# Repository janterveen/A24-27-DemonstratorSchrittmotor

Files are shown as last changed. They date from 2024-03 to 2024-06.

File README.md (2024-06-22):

<div>
  <p>
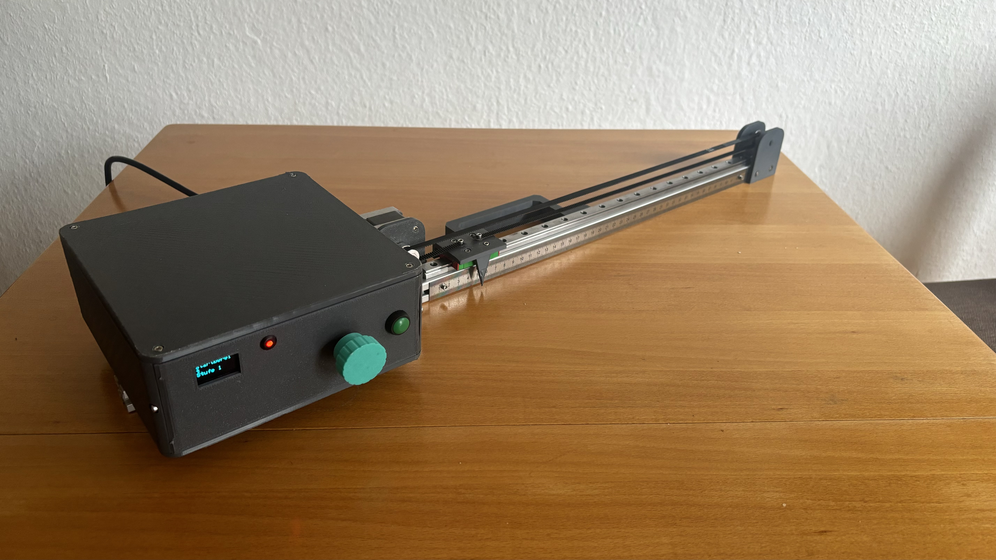
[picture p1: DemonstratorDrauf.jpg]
    
  </p>
  <b><h3> Automatisierungstechnik Projekt aus dem Jahr 2024 </h3></b>
  <p> Demonstrator für einen Schrittmotor mit <a href="https://www.arduino.cc"> Arduino-Ansteuerung </a></p>
</div>
<br>

# Betreuer: Prof. Dr. Elmar Wings

# Autoren (Name, Vorname, Matrikelnummer):

1. ter Veen, Jan, 7022071
2. Stein, Enno, 7021960
3. Theilmann, Maik, 7021861
4. Hanneken, Lars, 7021910
5. Grönke, Jannik, 7022006

# Projektbeschreibung: 
Die Aufgabe besteht darin, mithilfe eines Arduino Nano 33 BLE Sense Lite einen Demonstrator für einen Schrittmotor zu entwickeln. 
Mittels einer Konstruktion, die einen Schrittmotor beinhaltet, welcher einen Riemen antreibt, soll ein Schlitten auf einer Linearführung verfahren werden. 
Es sollen unterschiedliche Bewegungscharaketeristiken demonstriert werden. Der Schrittmotor wird über den Arduino angesteuert und in die gewünschte Richtung und Position bewegt. 

# Verzeichnisstruktur: 
## Autor, Projektplan und README
- [Author-Excel](author.xlsx)
  - Excel-Datei in der persönliche Daten über die einzelnen Gruppenmitglieder wiederzufinden sind
- [Projektplan-Excel](Projektplan.xlsx)
  - Excel-Datei die während des Projekts zur Projektplanung diente
- [README](README.md)
- [Evaluation](EvaluationHW.xlsx)

## Anhang
- [Konstruktion](DemonstratorSchrittmotor/Appendix/Konstruktion)
  - Sämtliche Zur Konstruktion benötigten Dateien, wie CAD-Dateien, G-Code und STL-Dateien
- [Material-Rückgabeliste](DemonstratorSchrittmotor/Appendix/MaterialRuekgabeListe)
  - Auflistung der nicht verwendeten Teilen
- [Mindmap](DemonstratorSchrittmotor/Appendix/Mindmap)
- [Schaltplan](DemonstratorSchrittmotor/Appendix/SchaltplanFritzing)

## Montageanleitung (sämtliche Inhalte und die verwendeten Bilder)
- [Montageanleitung](DemonstratorSchrittmotor/Assembly)
- [Inhalte](DemonstratorSchrittmotor/Assembly/Chapters)
  - Ort an dem sich die Tex-Dateien für die einzelnen Kapiteln der Montageanleitung befinden
- [Gestaltung](DemonstratorSchrittmotor/Assembly/General)
  - In diesem Ordner sind Dateien, zur Gestaltung der Montageanleitung
- [Bilder](DemonstratorSchrittmotor/Assembly/Images)
  - Ablage der Bilder, die in der Montageanleitung benutzt werden
- [PDF](DemonstratorSchrittmotor/Assembly/MontageAnleitung.pdf)

## verwendeter Code
- [Code](DemonstratorSchrittmotor/Code)
- [Arduino](DemonstratorSchrittmotor/Code/Arduino)
 - Testprogramm für den Arduino
- [DemonstratorSchrittmotor](DemonstratorSchrittmotor/Code/DemonstratorSchrittmotor)
 - Fertiges Programm für den Arduino
- [Encoder](DemonstratorSchrittmotor/Code/Encoder)
 - Testprogramm für den Encoder
- [html](DemonstratorSchrittmotor/Code/html)
 - Ordner für die doxygen Dokumentation
- [latex](DemonstratorSchrittmotor/Code/latex)
 - Ordner für die doxygen Dokumentation als Latex-Code
- [LED](DemonstratorSchrittmotor/Code/LED)
 - Testprogramm für die LED
- [OLEDDisplay](DemonstratorSchrittmotor/Code/OLEDDisplay)
 - Testprogramm für das OLED Display
- [Stepper](DemonstratorSchrittmotor/Code/Stepper)
 - Testprogramm für den Stepper
- [Taster](DemonstratorSchrittmotor/Code/Taster)
 - Testprogramm für den Taster
- [TastermitDebounce](DemonstratorSchrittmotor/Code/TastermitDebounce)
 - Testprogramm für den Taster mit Debounce

## Service- und Entwicklerdocumentation
- [Service- und Entwicklerdocumentation](DemonstratorSchrittmotor/DeveloperDoc)
- [Inhalte](DemonstratorSchrittmotor/DeveloperDoc/Chapters)
  - Ort an dem sich die Tex-Dateien für die einzelnen Kapiteln der Service- und Entwicklerdocumentation befinden
- [Gestaltung](DemonstratorSchrittmotor/DeveloperDoc/General)
  - In diesem Ordner sind Dateien, zur Gestaltung der Service- und Entwicklerdocumentation
- [Bilder](DemonstratorSchrittmotor/DeveloperDoc/Images)
  - Ablage der Bilder, die in der Service- und Entwicklerdocumentation benutzt werden
- [Tikz](DemonstratorSchrittmotor/DeveloperDoc/tikz)
  - Tex-Dateien zur Ersetllung von Tikz-Diagrammen oder Zeichnungen
- [Service- und Entwicklerdocumentation-PDF](DemonstratorSchrittmotor/DeveloperDoc/DemonstratorSchrittmotor.pdf)

## Demontageanleitung (sämtliche Inhalte und die verwendeten Bilder)
- [Demontageanleitung](DemonstratorSchrittmotor/Disassembly)
- [Inhalte](DemonstratorSchrittmotor/Disassembly/Chapters)
  - Ort an dem sich die Tex-Dateien für die einzelnen Kapiteln der Demontageanleitung befinden
- [Gestaltung](DemonstratorSchrittmotor/Disassembly/General)
  - In diesem Ordner sind Dateien, zur Gestaltung der Demontageanleitung
- [Bilder](DemonstratorSchrittmotor/Disassembly/Images)
  - Ablage der Bilder, die in der Demontageanleitung benutzt werden
- [PDF](DemonstratorSchrittmotor/Disassembly/DemontageAnleitung.pdf)
  
## verwendete Quellen und bib-file (Datenblätter und Literatur in PDF)
- [Dokumente](DemonstratorSchrittmotor/Documents)
- [Arduino IDE Dokumentation](DemonstratorSchrittmotor/Documents/ArduinoIDEDoku)
  - Quellen für die Softwaredokumentation von der Arduino Website
- [Datenblätter](DemonstratorSchrittmotor/Documents/Datenblätter)
  - Unter diesem Pfad befinden sich die Datenblätter, die für die Dokumentation benötigt wurden
- [Literatur](DemonstratorSchrittmotor/Documents/Literatur)
  - Hier befindet sich die verwendete Literatur
- [Bildquellen der Materialliste](DemonstratorSchrittmotor/Documents/MateriallisteQuellen)
- [Bibliothek](DemonstratorSchrittmotor/Documents/MyLiterature.bib)
  - Citavi Bibliothek mit allen genutzten Quelleinträgen

## Das Handbuch für den Demonstrator (sämtliche Inhalte und die verwendeten Bilder)
- [Handbuch](DemonstratorSchrittmotor/Manual)
- [Inhalte](DemonstratorSchrittmotor/Manual/Chapters)
  - Ort an dem sich die Tex-Dateien für die einzelnen Kapitel des Handbuches befinden
- [Gestaltung](DemonstratorSchrittmotor/Manual/General)
  - In diesem Ordner sind Dateien, zur Gestaltung des Handbuches
- [Bilder](DemonstratorSchrittmotor/Manual/Images)
  - Ablage der Bilder, die im Handbuch benutzt werden
- [Handbuch-PDF](DemonstratorSchrittmotor/Manual/HandbuchDemonstratorSchrittmotor.pdf)

## Das Poster zum Projekt (sämtliche Inhalte und die verwendeten Bilder)
- [Poster](DemonstratorSchrittmotor/Poster)
- [Bilder](DemonstratorSchrittmotor/Poster/images)
  - Ablage der Bilder, die im Poster benutzt werden
- [Poster-PDF](DemonstratorSchrittmotor/Poster/tikzposter.pdf)

## Literaturverzeichnis als Präsentation
- [Bilder](DemonstratorSchrittmotor/Presentations/images)
  - Coverbilder der Quellen
- [Hintergrundbilder](DemonstratorSchrittmotor/Presentations/img)
- [Folien](DemonstratorSchrittmotor/Presentations/slides)
- [Literaturverzeichnis-PDF](DemonstratorSchrittmotor/Presentations/Literaturverzeichnis.pdf)

## Schnelleinstieg
- [Schnelleinstieg-PDF](DemonstratorSchrittmotor/Presentations/Literaturverzeichnis.pdf)

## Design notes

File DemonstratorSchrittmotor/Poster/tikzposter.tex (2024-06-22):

%%%%%%
% $Beschreibung: Poster des Demonstrators mit erklärung eines Schrittmotors $
% $Autor: Groenke $
% $Datum: 18.06.2024 $
% $Version: 1 $
% $Pfad: SchrittmotorArduino/Poster/tikzposter.tex $
%
%%%%%%

\documentclass[25pt,a0paper, portrait]{tikzposter}
\usepackage[utf8]{inputenc}
\usepackage{xcolor}
\usepackage{graphicx,mwe}
\usepackage{filecontents}
\usepackage{lipsum}
\usepackage{tikz}
\usepackage{multicol}
\usepackage{adjustbox}
\usepackage{blindtext}
\usepackage{comment}

 \makeatletter
\def\TP@titlegraphictotitledistance{-6cm}
\settitle{ \centering \vbox{
		\@titlegraphic \\ [\TP@titlegraphictotitledistance] 
		\centering
		\color{titlefgcolor} 
		{\bfseries \Huge \sc \@title \par}
		\vspace*{1em}
		{\huge \@author \par}
}}
\makeatother

\setlength{\columnsep}{2cm}
 
\title{Schrittmotor Demonstrator}
\author{A24-27}
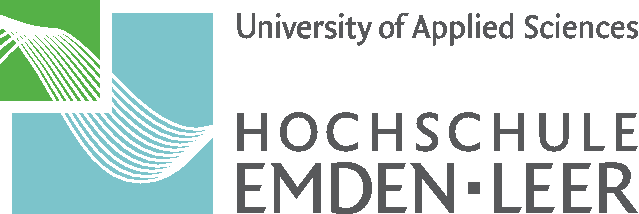
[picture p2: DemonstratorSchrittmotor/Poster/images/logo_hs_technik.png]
\titlegraphic{
	\hfill

}

\usetheme{Desert}
 
\begin{document}

\maketitle

\begin{columns} 
	
	\column{0.4}
	{
		\colorlet{blocktitlebgcolor}{blue}
		\block{Demonstrator für einen Schrittmotor}
		{
			\begin{tikzfigure}
				
			\end{tikzfigure}	
		}
		\block{Schrittmotoren}
		{
			Ein Schrittmotor ist ein Elektromotor, der sich für präzise Positionierungsaufgaben eignet. Im Gegenteil zu anderen Elektromotoren wird bei einem Schrittmotor keine Positionsmessung oder Positionsregelung benötigt. Mit diesem Motor ist eine erreichbare Positioniergenauigkeit von 0,1° möglich. Diese Art von Elektromotor wird beispielsweise in Druckern oder Scanner, aber auch im Kraftfahrzeugbereich verwendet. Im Kraftfahrzeugbereich werden die Schrittmotoren zur Spiegelverstellung sowie der Sitzverstellung verwendet. Das maximal erreichbare Drehmoment eines Schrittmotors liegt bei zwei Newtonmeter und die maximal erreichbare Drehzahl bei ca. 2000 Umdrehung pro Minute. Ein großer Vorteil des Schrittmotors ist seine Wartungsfreiheit, da der Rotor keine Wicklungen hat. [Babiel 2023, Hagl 2021]
		}
	}

	\column{0.6}
	{
		\colorlet{blocktitlebgcolor}{blue}
		\block{Projektbeschreibung}
		{
			Mithilfe eines Arduino Nano 33 BLE Sense Lite wurde dieser Demonstrator für einen Schrittmotor entwickelt. Mittels einer Konstruktion, die über einen Schrittmotor verfügt, wird ein Riemen angetrieben. An diesem Riemen ist ein Schlitten befestigt, der durch die Bewegung des Schrittmotors auf einer Linearführung verfahren wird. An dem Gehäuse befindet sich ein Drehschalter, mit dem eine von zehn Bewegungsstufen ausgewählt werden kann. Nach der Auswahl kann das Programm über den grünen Start-Stopp-Knopf gestartet werden. Die Status-LED leuchtet rot, sobald das Gerät einsatzbereit ist. Für die Referenzfahrt wurde ein Endschalter an der Halterung des Schrittmotors befestigt, damit der Schrittmotor auf eine definierte Position referenzieren kann. Es gibt zehn verschiedene Bewegungsstufen. Die Bewegungsstufen unterscheiden sich in der Geschwindigkeit. Pro Stufe wird die Geschwindigkeit erhöht.
			Ein großer Teil der Bauteile wurde mit einem 3D-Drucker gefertigt. So konnten Gehäuse, Drehschalter, Zeiger (auf dem Schlitten), Halterungen, sowie ein Griff selbst konstruiert und angepasst werden. 
		}
		\block{Nema 17 Schrittmotor}
		{
			Für dieses Projekt wird ein Nema 17 Schrittmotor der Firma Creality3D verwendet. Dieser Schrittmotor wird im 3D-Druck sowie in CNC-Maschinen eingesetzt. Der Motor arbeitet im Bipolarbetrieb und es sind zwei Spulen verbaut. Er hat einen Schrittwinkel von 1,8 ° und
			benötigt somit 200 Schritte für eine volle Umdrehung. Die Wellenlänge beträgt 20 mm und der Wellendurchmesser 5 mm. Der ausgewählte Schrittmotor arbeitet mit einer Nennspannung von 12 Volt. Dadurch, dass er mit einer niedrigen Spannung arbeitet, kann kein hohes Drehmoment erzeugt werden. Allerdings erzielt der Schrittmotor eine gute Positioniergenauigkeit durch den kleinen Schrittwinkel und die Microstepp-Funktion. Des Weiteren arbeitet der Motor mit 0,84 Amper pro Phase. Weitere Vorteile des Schrittmotors sind die kompakte Bauform mit den Abmessung 42 x 42 x 34 mm sowie die geringe Masse von 220 Gramm. Betrieben werden kann der Schrittmotor in einer Umgebungstemperatur von -20 °C bis +50 °C. [Gemsmotor 2024] 
		}
	}
\end{columns}

\begin{columns} 
	
	\column{0.4}
	{
		\colorlet{blocktitlebgcolor}{blue}
		\block{Nema 17 Schrittmotor}
		{
			\begin{tikzfigure}
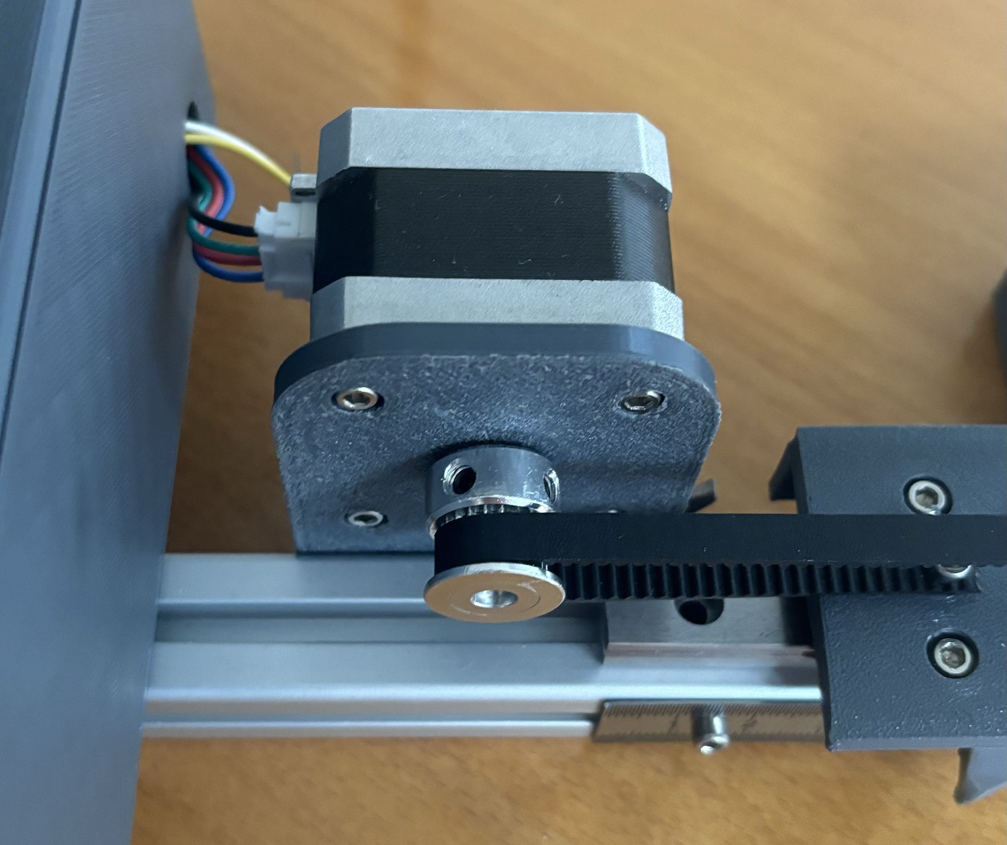
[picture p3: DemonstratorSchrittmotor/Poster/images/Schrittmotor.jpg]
				
			\end{tikzfigure}	
		}
		\block{Quellen}
		{
			\begin{itemize}
				\item R. Hagl. Elektrische Antriebstechnik. 3., überarbeitete und erweiterte Auflage. München: Hanser, 2021. isbn: 978-3-446-46572-5.
				\item G. Babiel. Elektrische Antriebe in der Fahrzeugtechnik: Lehrund Arbeitsbuch. 5. Auflage. Wiesbaden und Heidelberg: Springer Vieweg, 2023. isbn: 978-3-658-40585-4.
				\item Gemsmotor. Nema 17-Datasheet.
			\end{itemize}
		}
	}

	\column{0.6}
	{
		\colorlet{blocktitlebgcolor}{blue}
		\block{Herausforderungen}
		{
			Das Projekt lässt sich in drei verschiedene Teilprojekte unterteilen, die zum Abschluss der Aufgabe führen. Zuerst ist da die Konstruktion des Demonstrators und die hierfür benötigte Auswahl der Hardware-Teile. Vorgabe war, dass der Aufbau nicht zu komplex ist und man sich so auf die wesentlichen Teile konzentriert. Außerdem ist die Arbeit mit der Arduino IDE und die Programmierung des Arduino ein weiterer Teil. Als letzten Punkt ist der Umgang mit den elektronischen Bauteilen zu erwähnen. Der Umgang mit den elektronischen Bauteilen sollte unter großer Vorsicht geschehen, sodass diese nicht durch den elektrischen Strom beschädigt werden.
		}
		\block{Lösungsansatz}
		{
			Durch die Ausarbeitung der Herausforderungen, können Lösungsansätze	entwickelt werden. Vorab wurde eine erste Konzeptskizze angefertigt, aus der Ideen entstanden. Im ersten Konzept sollte der Schrittmotor eine Plattform über einen Riementrieb axial verfahren. Dabei sollte der Verfahrweg der Plattform über einen Abstandssensor mit einem vorher definierten Abstand zu einem Objekt, geregelt werden. Wird das Objekt näher oder weiter entfernt vom Abstandssensor bewegt, verfährt die Plattform mit einem definierten Abstand mit. Alle vorhandenen Bauteile sollten an einem Alu-Profil befestigt werden. Aufgrund der hohen Komplexität wurde die Plattform inklusive des Abstandssensors, aus dem zweiten Konzept entfernt. Stattdessen wird auf dem Schlitten der Linearführung, ein Zeiger und auf dem Alu-Profil, ein Lineal integriert. Mittels verschiedener Stufen soll der Schrittmotor unterschiedliche Geschwindigkeiten demonstrieren. Gegenüber dem zweiten Konzept wurde die Hardware aus Transportiergründen mit auf dem Aluprofil verlegt und erhielt zum Schutz ein Gehäuse.
		}
		\block{Zukünftige Projekte}
		{
			\begin{itemize}
				\item Aktive Geschwindigkeits- und Beschleunigungsregelung durch Beschleunigungssensor
				\item Manuelle Eingabe von Beschleunigung und Geschwindigkeit
				\item Manuelle Eingabe des Verfahrweges
			\end{itemize}
		}
	}
\end{columns}

\end{document}

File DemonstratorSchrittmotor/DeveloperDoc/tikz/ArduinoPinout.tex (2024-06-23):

%%%%%%
%
% $Autor: ter Veen $
% $Datum: 01.06.2024 $
% $Version: 1 $
% $Pfad: SchrittmotorArduino/DevoloperDoc/tikz/ArduinoPinout.tex $
%
%%%%%%
	\begin{tikzpicture}[scale=2]
		% Arduino Dummy
		\draw[fill=blue!20] (0,0) rectangle (6,3);
		
		% Pin Beschriftung oben
		\foreach \x in {0.375,1.125,...,5.625}
		\draw (\x,3) -- (\x,3.5) node[above] {};
		\foreach \x in {0.75,1.5,...,5.25}
		\draw (\x,3) -- (\x,3.25) node[above] {};
		
		% Pin Beschriftung unten
		\foreach \x in {0.375,1.125,...,5.625}
		\draw (\x,0) -- (\x,-0.5) node[below] {};
		\foreach \x in {0.75,1.5,...,5.25}
		\draw (\x,0) -- (\x,-0.25) node[below] {};

		% Pins oben
		\node at (0.375,3.65) {D12};
		\node at (0.75,3.35) {D11};
		\node at (1.125,3.65) {D10};
		\node at (1.5,3.35) {D9};
		\node at (1.875,3.65) {D8};
		\node at (2.25,3.35) {D7};
		\node at (2.625,3.65) {D6};
		\node at (3,3.35) {D5};
		\node at (3.375,3.65) {D4};
		\node at (3.75,3.35) {D3};
		\node at (4.125,3.65) {D2};
		\node at (4.5,3.35) {GND};
		\node at (4.875,3.65) {RESET};
		\node at (5.25,3.35) {RX};
		\node at (5.625,3.65) {TX};
		
		% Pins unten
		\node at (0.375,-0.65) {D13};
		\node at (0.75,-0.4) {+3V3};
		\node at (1.125,-0.65) {AREF};
		\node at (1.5,-0.4) {A0};
		\node at (1.875,-0.65) {A1};
		\node at (2.25,-0.4) {A2};
		\node at (2.625,-0.65) {A3};
		\node at (3,-0.4) {A4};
		\node at (3.375,-0.65) {A5};
		\node at (3.75,-0.4) {A6};
		\node at (4.125,-0.65) {A7};
		\node at (4.5,-0.4) {+5V};
		\node at (4.875,-0.65) {RESET};
		\node at (5.25,-0.4) {GND};
		\node at (5.625,-0.65) {VIN};
		
		% Dummys zur Orientierung
	
		\draw[fill=gray!30] (4,0.5) rectangle (5.5,2.5) node[pos=0.5, align=center] {Bluetooth-\\Modul};
		\draw[fill=green!30] (5.5,0.5) rectangle (6,2.5) node[pos=0.5, align=center] {};
		\draw[fill=gray!30] (-0.5,0.7) rectangle (1,2.3) node[pos=0.5, align=center] {USB};
		\draw[fill=white] (0.1,2.9) circle (0.075) node[right=1mm]{};
		\draw[fill=white] (0.1,0.1) circle (0.075) node[right=1mm]{};
		\draw[fill=white] (5.9,0.1) circle (0.075) node[right=1mm]{};
		\draw[fill=white] (5.9,2.9) circle (0.075) node[right=1mm]{};
		
		% LED´s
		\draw[fill=green] (0.25,2.5) circle (0.1) node[right=3mm] {Power-LED};
		\draw[fill=orange] (0.25,0.5) circle (0.1) node[right=3mm] {RGB-LED};
		\draw[fill=blue!40] (3.5,2) circle (0.1) node[above=4mm] {RGB-LED};
		
	\end{tikzpicture}

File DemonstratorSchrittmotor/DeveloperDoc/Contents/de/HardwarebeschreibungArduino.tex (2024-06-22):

%%%%%%%%%%%%%%%%%%%%
%
% $Beschreibung: Dieser Abschnitt enthält alle Informatioenen explizit zur Hardware des Arduino Nano 33 BLE Sense Lite $
% $Autor: ter Veen $
% $Datum: 14.06.2024 $
% $Pfad: DemonstratorSchrittmotor/DeveloperDoc/Contents/de/HardwarebeschreibungArduino.tex $
% $Version: 6 $
%
%
%%%%%%%%%%%%%%%%%%%

\chapter{Hardwarebeschreibung des Arduino}
\begin{figure}[htb]
		\input{tikz/ArduinoNano33BLESense}
		\caption{Arduino Nano 33 BLE Sense (Vereinfachte Darstellung)} \label{ArduinoNano33BLESense1}
		\begin{tabularx}{\textwidth}{|p{1.5cm}|X|}
			\hline
			\textbf{Pos.Nr.} & \textbf{Modul/Sensor} \\
			\hline
			P1 & Mikrophone \\
			\hline
			P2 & 9-Achs-IMU \\
			\hline
			P3 & Näherungs-,Umgebungslicht-, Farb- und Gestensensor \\
			\hline
			P4 & Drucksensor \\
			\hline
			P5 & Bluetooth-Modul \\
			\hline
		\end{tabularx}
		\captionof{table}{Arduino Nano 33 BLE Sense \cite{Ard.2024}} \label{ArduinoNano33BLESense2}
\end{figure}

\section{Aufbau des Arduinos}

Der Arduino Nano 33 \ac{ble} Sense Lite ist ein Mikrocontroller basierend auf dem Nordic nRF52840-\ac{soc}. Trotz seiner kompakten Bauweise mit einer Größe von 45 x 18 mm verfügt es über mehrere verschiedene integrierte Sensoren, Aktoren und Anschlussschnittstellen (siehe \autoref{ArduinoNano33BLESense1}). Darüber hinaus verfügt der Arduino-Prozessor über 1 MB Flash-Speicher und 256 KB RAM. Bei dem Prozessor handelt es sich um einen Arm\textregistered Cortex-M4F Prozessorkern, welcher mit einer Taktrate von 64 MHz arbeitet und für Mikrocontroller Anwendungen optimiert ist. Dieser bietet eine gute Leistung bei geringen Stromverbrauch und ist auch für Echtzeit-Verarbeitungsaufgaben geeignet. Außerdem besitzt der Prozessor eine \ac{fpu}, die eine effiziente Abarbeitung von Datenverarbeitungsoperationen ermöglicht. Mit Hilfe einer integrierten Steckverbindung (engl. \glqq header \grqq) kann der Mikrocontroller direkt auf ein Board gesteckt werden. \cite{Arm.2020} \cite{Ard.2024}

\section{Integrierte Sensorik}

Der Arduino Nano 33 \ac{ble}-Sense Lite verfügt über eine Vielzahl von integrierten Sensoren und Aktoren, mit denen verschiedene Umgebungseigenschaften erfasst werden können. Dazu gehören die in den folgenden Abschnitten beschriebenen Sensoren und Aktoren.

\subsection{9-Achs-IMU für die Bewegungserkennung (LSM9DS1)}\label{9Achs}

Bei der Inertialmesseinheit LSM9DS1 handelt es sich um ein System-in-Package, d.h. es sind mehrere elektronische Komponenten bzw. Chips auf kleinstem Raum in einem Gehäuse kombiniert.\cite{Lienig.2012} Die \ac{imu} verfügt über einen 3D-Linearbeschleunigungsmesser, ein 3D-Gyroskop und einen 3D-Magnetometer. Darüber hinaus verfügt das System über eine serielle \ac{i2c}-Busschnittstelle, die einen Standard und einen Fast Mode (100/400 kHz) bereitstellt, zudem eine serielle SPI-Standardschnittstelle. Der Sensor verfügt über einen linearen Beschleunigungsmesser (Accelerometer) mit wählbarer Skala von ±2/±4/±8/±16 g, der die lineare Beschleunigung in drei Achsen (x, y, z)misst und die Erfassung von Geschwindigkeits- und Positionsänderungen ermöglicht. Das Magnetfeld ist mit einer wählbaren Skala von ±4/±8/±12/±16 Gs ausgestattet, damit misst es das magnetische Feld in den drei Achsen und ermöglicht die Bestimmung der Ausrichtung relativ zur Erdmagnetfeldrichtung. Das 3D-Gyroskop ist mit einem wählbarem Skalenendwert von: ±125/±250/±500/±1000/±2000 $\frac{Grad}{s}$ ausgestattet und ist für die Erfassung der Winkelgeschwindigkeit bzw. Drehbewegung um die drei Achsen zuständig.\cite{STM1.2015}\cite{Ard.2024}
Mögliche Anwendungsbereiche sind zum Beispiel eine Bewegungssteuerungen (Drohnensteuerung, Robotik und industrielle Automatisierung), Schwingungsüberwachung und -kompensation, Antennen, Plattformen, optische Bild- und Objektivstabilisierung.  

\subsection{Näherungs-,Umgebungslicht-, Farb- und Gestensensor (APDS9960)}

Hierbei handelt sich um einen sehr vielseitigen Sensor. Er dient zur Gestenerkennung, Farberkennung, Abstandsmessung und Umgebungslichtmessung. Die Gestenerkennung nutzt vier gerichtete Fotodioden, um reflektierte Infrarot-Energie (von der integrierten \ac{led}) zu erfassen, um physikalische Bewegungsinformationen (d.h. Geschwindigkeit, Richtung und Entfernung) in digitale Informationen zu übersetzen. Die Näherungserkennung ermöglicht die Messung der Entfernung durch die Erkennung der reflektierten Infrarot-Energie, (von der integrierten \ac{led}) mit Hilfe einer Fotodiode. Erkennungsereignisse sind interruptgesteuert und treten immer dann auf, wenn das Näherungsergebnis die oberen und/oder unteren Schwellenwerte überschreitet. Der Sensor verfügt außerdem über Offset-Einstellregister zur Kompensation des System-Offsets, der durch unerwünschte Infrarot-Energiereflexionen am Sensor verursacht wird. Die Intensität der Infrarot-LED wird werkseitig eingestellt, so dass eine Kalibrierung der Endgeräte aufgrund von Bauteilschwankungen nicht erforderlich ist. Die Farb- und Umgebungslichterkennung liefert Daten zur roten, grünen, blauen Farbspektrum und Daten zum klaren Lichtintensität. Jeder der Kanäle R, G, B, C verfügt über einen \ac{uv}- und Infrarot-Sperrfilter und einen speziellen Datenkonverter, der gleichzeitig 16-Bit-Daten erzeugt. Diese Architektur ermöglicht Anwendungen eine genaue Messung des Umgebungslichts zu messen und die Farbe zu erkennen, was es den Geräten wiederum ermöglicht, die Farbtemperatur zu berechnen und die Hintergrundbeleuchtung des Displays dementsprechend anzupassen.\cite{AT.2015}\cite{Ard.2024}
	
\subsection{Barometrischer Drucksensor (LPS22HB)}

Der LPS22HB ist ein sehr kompakter Absolutdrucksensor, der auf dem piezoresistiven Prinzip basiert. Er arbeitet als Barometer und verfügt über einen digitalen Ausgang. Zudem ist in diesem Drucksensor ein Temperatursensor integriert, mit welchem Druckmessungen zusätzlich kompensiert werden können. Das Gerät besteht aus einem Sensorelement und einer \ac{ic}-Schnittstelle, die eine Kommunikation zwischen der Sensoreinheit und der Anwendung über \ac{i2c} oder \ac{spi} ermöglicht. Das Sensorelement erfasst den absoluten Druck und besteht aus einer speziell gefertigten, hängenden Membran. Der LPS22HB ist in einem vollständig vergossenem Land-Grid-Array-Gehäuse untergebracht, das kleine Löcher aufweist. Durch diese Öffnung gelangt der externe Druck auf das Sensorelement. Der Betrieb des Sensors ist über einen Temperaturbereich von -40 °C bis +85 °C gewährleistet. \cite{STM2.2017}\cite{Ard.2024}
Anwendungsbereiche für diesen Sensor sind zum Beispiel: Wetterstationen, Höhenmesser, Luftdrucküberwachung in industriellen Prozessen oder tragbare smarte Geräte, wie Sportuhren oder Smartphones.
	
\subsection{Digitales Mikrophon (MP34DT05)}

Das MP34DT05-A ist ein kompaktes, stromsparendes, omnidirektionales, digitales
Mikrofon mit einem kapazitiven Sensorelement und einer \ac{ic}-Schnittstelle.
Das Sensorelement, das in der Lage ist, akustische Wellen zu detektieren, wird mit einem speziellen Silizium-Mikrobearbeitungsverfahren für die Herstellung von
Audiosensoren hergestellt. Die \ac{ic}-Schnittstelle wird in einem speziellen Halbleiterherstellungsverfahren (CMOS-Verfahren\cite{Gehrke.2022}\cite{Bernstein.2020}) hergestellt, das die Entwicklung einer speziellen Schaltung ermöglicht, die ein digitales Signal im \ac{pdm}-Format extern bereitstellen kann. Das Mikrofon hat einen Signal-Rausch-Abstand von 64 dB und eine Empfindlichkeit von -26 dBFS ±3 dB. Sein maximaler Schalldruckpegel liegt bei 122,5 dBSPL. Der MP34DT05-A ist in einem \ac{smd}-kompatiblen, \ac{emi}-geschirmten Top-Port-Gehäuse erhältlich und arbeitet zuverlässig über einen erweiterten Temperaturbereich von -40 °C bis +85 °C. Abmessungen des Gehäuses HCLGA-4 LD sind $3\times 4 \times 1$ (in mm). Anwendung findet das Modul Beispielsweise in mobilen Endgeräten, im Bereich der Spracherkennung sowie in Laptops und Notebooks.\cite{STM3.2021}\cite{Ard.2024}

\subsection{DC-DC-Wandler (MPM3610)}

Das MPM3610-Modul ist ein integriert Gleichspannungs- zu Gleichspannungs-Wandler. Dieser kann Eingangsspannungen von bis zu 21\ V verarbeiten mit einem Wirkungsgrad von mindestens 65\% bei minimaler Last. Bei einer Eingangsspannung erhöht sich der Wirkungsgrad auf 85\%.\cite{Ard.2024}

\section{Beschreibung der Schnittstellen}

Der Arduino Nano 33 \ac{ble}-Sense Lite bietet eine Vielzahl von Schnittstellen (siehe \autoref{arduinopinout}), die das Board mit anderen Komponenten und Geräten einfach verbinden lassen. In diesem Abschnitt sind einige Details zu den wichtigsten Schnittstellen des Boards erläutert.

	\begin{figure}
		\input{tikz/ArduinoPinout}
		\caption{Arduino Nano Pinbelegung \cite{Ard.2024}}
		\label{arduinopinout}
	\end{figure}

\subsection{I\textsuperscript{2}C}

Der \ac{i2c}-Bus ermöglicht die geräteinterne Kommunikation von Mikrocontrollern mit Sensoren, externen Bildschirmen, Echtzeituhren und vielen anderen Bausteinen. Das Kommunikationsprotokoll basiert auf dem Master-Slave-Prinzip. Der Master initiiert und beendet die Kommunikation, stellt den Takt zur Synchronisation bereit und löst Kommunikationsprobleme. Jeder Slave hat eine eindeutige Adresse, mit einer Länge von 7 oder 10 Bit und ermöglicht die Adressierung von bis zu 128 bzw. 1024 unterschiedlichen Slaves in dem selben Bus. Geräte mit unterschiedlichen Adresslängen können im selben Bus koexistieren. Bevor der Master Daten überträgt oder empfängt, muss er einen Slave mit einer vorher vereinbarten Adresse ansprechen.\cite{Meroth.2021}\cite{STM1.2015}\cite{Bernstein.2020} Sind ihre Adressen in Übereinstimmung kann im nächsten Schritt ein einzelnes Bit gesendet werden, mit dem dann festgelegt wird, ob der Master Daten an dem Slave übertragen (Binär:1) oder auslesen möchte (Binär:0). Dieser Datenaustausch wird danach bestätigt, sodass weitere Daten ausgetauscht werden können. Zur Beendigung des Datenaustausches wird ein Stop-Signal gesendet.\cite{Gehrke.2022} In der minimalen Konfiguration werden Master und Slave über die bidirektionalen Busleitungen \ac{sda} und \ac{scl} verbunden, die über Pull-up-Widerstände an die Versorgungsspannung angeschlossen sind. Weitere Geräte können durch Verbindung ihrer \ac{sda}- und \ac{scl}-Anschlüsse mit den entsprechenden Busleitungen an den Bus angeschlossen werden.\cite{Meroth.2021} In diesem Projekt dient der Arduino als Master und ein zusätzlich angeschlossenes \ac{oled}-Bildschirm als Slave.

\subsection{USB}

Das Board kann über einen \ac{musb} mit einem Computer verbunden werden, um es zu programmieren oder Daten zu übertragen. Die Datenübertragungsrate beträgt dabei 12 Mbit/s. Außerdem kann der Arduino über diesen \ac{musb}-Port Strom beziehen.

\subsection{Bluetooth\textregistered 5}

Die Bluetooth-Verbindung kann als drahtloser Kommunikationsweg eingesetzt werden. Das Bluetooth-Protokoll hat eine Übertragungsrate von 2 Megabit pro Sekunde (Mbps) und eine Sendeleistung von +8 Dezibel Milliwatt (dBm). Die Empfindlichkeit beträgt dabei -95 dBm. Des weiteren verbraucht diese Verbindung im Sendebetrieb 4,8 mA und 4,6 mA im Empfangsbetrieb. Das Bluetooth-Modul ist kompatibel mit mehreren Protokollen, unter anderem mit dem \textit{Thread-Protokoll} und dem \textit{Zigbee-Protokoll}.\cite{Ard.2024} \cite{NrdSem4.2024}

\subsection{Weitere Kommunikationsschnittstellen}
\cite{Ard.2024}
	\begin{itemize}
		\item \textbf{NFC-A-Tag:} \ac{nfc} ist eine zusätzliche Funktion zur drahtlosen Kommunikation über kurze Distanzen. Zudem besitzt der \ac{nfc}-A-Tag die Funktionen, sich in einen Bereitschaftsmodus versetzen zu lassen, dass durch ein \ac{nfc}-fähiges Gerät dann initiiert werden kann. Außerdem unterstützt es \textit{touch-to-pair}, diese Funktion ermöglicht eine Kopplung mit anderen \ac{nfc}-fähigen Geräten durch Berührung.
		\item \textbf{Arm CryptoCell CC310 Security Subsystem:} Für die Durchführung kryptografischer Operationen und Sicherheitsaufgaben.\\ \cite{NrdSem.2024}
		\item \textbf{QSPI/SPI/TWI/$I^2$S/PDM/QDEC:} Verschiedene weitere serielle Kommunikationsschnittstellen, die für den Datenaustausch verwendet werden können.
		\item \textbf{EasyDMA:} \ac{dma} ist für die Übertragung von Daten zwischen verschiedenen Speicherbereichen, ohne dabei die CPU zu belasten.\cite{Gehrke.2022}
		\item \textbf{\ac{adc}):} Wandelt analoge Eingangsignale in digitale Daten um. Der Wandler hat eine Auflösung von 12 Bit und eine maximale Abtastrate von 200 Kilosamples pro Sekunde (ksps).
		\item \textbf{128-Bit-AES/ECB/CCM/AAR-Co-Prozessor:} Co-Prozessor für kryptografische Operationen, der auf dem \ac{aes} basiert. Dieser unterstützt verschiedene Betriebsmodi wie \ac{ecb}, \ac{ccm} und \ac{aar}. \cite{NrdSem2.2024}
		\item \textbf{Quad-SPI-Schnittstelle 32 MHz:} \ac{spi}-Schnittstelle, die eine maximale Taktrate von 32 MHz unterstützt. Quad-SPI ermöglicht es, Daten schneller als die herkömmliches SPI zu übertragen, indem es vier Datenleitungen verwendet.\cite{NrdSem3.2023}
	\end{itemize}

\subsection{Digitale Ein- und Ausgangspins}

Das Board verfügt über 14 digitale Ein- und Ausgangspins. Die digitalen Pins können nur zwei Zustände, nach dem Binär-System lesen: wenn ein Spannungssignal vorliegt und wenn kein Signal vorhanden ist (0 oder 1). Einige der Pins sind zudem zur Pulsweitenmodulation fähig (D3, D5, D6, D9, D10). Außerdem sind die digitalen Pins D11 und D12 als Master-Output-Slave-Input (MOSI) und als Master-Input-Slave-Output (MISO), in einer Serial-Peripheral-Interface (SPI) Kommunikation einsetzbar.\cite{Ard.2024}

\subsection{Analoge Eingangspins}

Die Platine hat zusätzlich 8 analoge Eingangspins (A0-A7), die wiederum als Analog-Digital-Wandler (ADC) verwendet werden können. Außerdem sind diese Pins als digitale Ein-/Ausgangspins konfigurierbar. Der Pin A0 kann zudem als Digital-Analog-Wandler (DAC) konfiguriert werden. Die beiden Pins A4 und A5 können außerdem für die I2C-Kommunikation verwendet werden. Dabei fungiert A4 als Datenleitung (SDA), während A5 als Taktleitung (SCL) fungiert.\cite{Ard.2024}

\subsection{Weitere Pins}
	\begin{itemize}
		\item \textbf{+3,3 V}: Erzeugt interne Stromquelle im Gerät und wird als Referenzspannung verwendet.
		\item \textbf{VIN}: Stromversorgung
		\item \textbf{5V}: Gibt 5V an die externen Komponenten ab. 
		\item \textbf{RST-Pin}: Dient zum Zurücksetzen des Arduinos.
		\item \textbf{AREF-Pin}: Liefert die Spannungsreferenz, die der Mikrocontroller zur Zeit verwendet.
		\\ \cite{Ard.2024}
	\end{itemize}

\subsection{LED-Lampen}

Im Arduino selbst sind 3 LED´s verbaut, die auch alle programmiert werden können. Diese sind vor allem für die Überprüfung der Sensorik oder Softwareprogrammen nützlich. Zu den LED-Lampen gehören: 
	\begin{itemize}
		\item Programmierbare Power-LED (grün): Zeigt an, dass das Arduino-Board eingeschaltet ist.
		\item Programmierbare LED (orange)
		\item Programmierbare RGB-LED
		\\ \cite{Ard.2024}
	\end{itemize}

\section{Hinweis Arduino 33 BLE Sense Lite \label{Hinweis Arduino 33 BLE Sense Lite}}

Der Arduino Nano 33 BLE Sense \underline{Lite} ist eine komprimierte Variante vom ursprünglichen Arduino Nano 33 BLE Sense, welcher zusätzlich noch über einen Temperatur- und Feuchtigkeitssensor verfügt. Der Lite hat stattdessen einen Drucksensor integriert, über welchem auch die Temperatur gemessen werden kann, jedoch nicht die Feuchtigkeit.\cite{PetrFilipi.2022}

\section{Bezugsquellen}

Als Bezugsquellen dienten vor allem Datenblätter der Hersteller. Die meisten Informationen konnten dem Datenblatt des Arduino entnommen werden, jedoch ist dazu anzumerken, dass sich dieses Datenblatt auf den Arduino 33 BLE Sense bezieht und nicht auf den Arduino 33 BLE Sense \emph{Lite}. Speziell zum \emph{Lite} gibt es jedoch kein Datenblatt, so wurde das Datenblatt vom Arduino 33 BLE Sense herangezogen. Dies stellt sonst kein Problem dar, da sich, wie in \ref{Hinweis Arduino 33 BLE Sense Lite} beschrieben, nur um eine komprimierte Version des Arduino 33 BLE Sense handelt.

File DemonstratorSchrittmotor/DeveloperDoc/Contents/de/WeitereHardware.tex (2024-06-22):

%%%%%%%%%%%%%%%%%%%%
%
% $Beschreibung: Beschreibung der zusätzlich benötigten Hardware (zus. zum Arduino und Schrittmotor) für den Aufbau $
% $Autor: Theilmann und ter Veen $
% $Datum: 15.06.2024 $
% $Pfad: DemonstratorSchrittmotor/DeveloperDoc/Contents/de/WeitereHardware.tex $
% $Version: 4 $
%
%
%%%%%%%%%%%%%%%%%%%

\chapter{Weitere Hardware}

In den folgenden Kapiteln werden die wichtigsten zusätzlich benötigten Hardwarekomponenten aufgelistet und erläutert. Dazu zählen Aktoren zur Darstellung des Betriebszustandes, Schalter und weitere Komponenten, die für den Aufbau des Schrittmotor-Demonstrators nötig waren.  

\section{OLED-Display}

Zur Feststellung des aktuellen Betriebszustandes und zur Ausgabe der eingestellten Bewegungsstufe des Schlittens dient ein 1,3\ Zoll OLED-Display \emph{(Organic Light Emitting Diode)}. Bei OLED-Displays sind jeweils drei OLEDs für einen Bildpunkt zuständig und benötigen keine Hintergrundbeleuchtung oder LC-Zellen, wodurch ein scharfer Kontrast möglich ist. OLED-Displays zeichnen sich durch die Reaktionsschnelligkeit aus. Die Helligkeit eines Pixels wechselt in weniger als einer Mikrosekunde.\cite{DieterStotz.2019} Insgesamt ist das Modul $36 \ mm \times 34  \ mm \times36 \ mm$ groß mit einer Bildschirmdiagonalen von $1,3\ Zoll $. Das Display besteht aus $128 \times 64 \ $ weißen OLED-Bildpunkten. Durch die \ac{i2c}-Kommunikation kann das Display mit dem Arduino verbunden werden. Zur Stromversorgung wird  3,3\ V Gleichstromspannung, bei einem Stromverbrauch von weniger als 11\ mA, benötigt. Mithilfe von 4 Steckbrückenkabel ist es mit dem Arduino verbunden, um es mit der nötigen Spannung zu versorgen und die \ac{i2c}-Verbindung herzustellen (Verdrahtung detailliert in Kapitel \ref{MLLS} \nameref{MLLS}). Die zur \ac{i2c}-Kommunikation nötige Adresse ist 0x3F. 
Zusätzliche Spezifikationen des Displays sind: 
	\begin{itemize}
		\item Pixelgröße: $0.21 \ mm \times 0,21 \ mm $
		\item Pixelabstand: $0.23 \ mm \times 0,23 \ mm $
		\item Anzeigemodus: Passive Matrix
		\item Pixelfarbe: Blau
	\end{itemize}
\cite{AZDelivery.2024}

\section{Signalleuchte}

Zusätzlich zum OLED-Display ist eine SMD-LED-Signalleuchte zur Zustandserkennung verbaut. Sie soll Störungen und Fehler erkenntlich machen. SMD steht für \emph{Surface Mount Device} und bedeutet, dass die Signalleuchte für Oberflächenmontagen konzipiert ist. Die Leuchte ist dabei mit einem einfachen Stecksystem am Gehäuse befestigt. Dazu wird sie in einer 8\ mm Montagebohrung des Gehäuses gesteckt und über die 10\ mm Gehäuseblende der Signalleuchte fixiert. Die Leuchte hat eine 3\ mm im Durchmesser große LED und emittiert ein rotes Licht. Die Betriebsspannung liegt zwischen 2 bis 2,4\ V und der Betriebsstrom bei 20\ mA. Angeschlossen wird sie über vier Litzen am Arduino (siehe \ref{MLLS} \nameref{MLLS}).\cite{Mentor.2024}

\section{Spannungswandler}

Für den Aufbau des Demonstrators sind mehrere Spannungswandler benötigt. Folgende Wandler wurden in der Schaltung verwendet.

\subsection{Netzteil SNT RD 50A}

Dieser Wechselspannung-/Gleichspannungswandler (AC/DC-Wandler) wandelt die 230\ V Wechselspannung des Netzanschlusses in 12\ V  und 5\ V Gleichspannung um. 
Weitere Spezifikationen des Wandlers sind:
\begin{itemize}
	\item \textbf{Bauteilabmessung ($L\times B \times H$):} $99 \ mm \times 97 \ mm \times 36 \ mm$
	\item \textbf{Ausgangsstrom:} 2\ A
	\item \textbf{Leistung:} 54\ W
	\item \textbf{Wirkungsgrad:} 79\ \% 
\end{itemize} 
\cite{Meanwell.2019}

\subsection{Spannungswandler ASM1117}

Dieser Spannungswandler wandelt die 5\ V des Netzteils SNT RD 50A in jeweils 3,3\ V. Die 3,3\ V werden für den Arduino, Schrittmotorsteuerung, OLED-Display und dem Drehwinkel-Encoder verwendet. Weitere Technische Daten des Wandlers sind:
\begin{itemize}
	\item \textbf{Bauteilabmessung ($L\times B \times H$):} $40 \ mm \times 40 \ mm \times 20 \ mm$
	\item \textbf{Ausgangsstrom:} 800\ mA
\end{itemize}
	\cite{AMS.2024}
	
\section{Linearführung}

Zur Demonstration einer Linearbewegung wird eine kompakte Linearführung verwendet. Die Führung ist 450\ mm lang und 12\ mm breit. Diese Linearführung wird vor allem in Fused Deposition Modeling (FDM) -Drucker verwendet, wo es auf hohe Präzision bei niedrigen Toleranzen ankommt. Daher ist diese Führung auch für dieses Projekt gut geeignet, bei dem es nicht darum geht, große Lasten zu bewegen, sondern die Schrittauflösung möglichst genau auf die Millimeterskala zu übertragen.\cite{RoboterBausatz.2024}

\section{Drehwinkel-Encoder}

Der Demonstrator soll mehrere Programme fahren können, deswegen wurde ein Drehwinkel-Encoder der Steuerung hinzugefügt. Dieser wird über drei Pins am Arduino angeschlossen und über zwei weitere Pins wird er mit Spannung versorgt. Durch drehen des Drehschalters werden nacheinander drei Kontakte geschlossen oder geöffnet (ein Kontakt ist immer geschlossen). Dieser dadurch entstehende Signalfluss, bestehend aus zwei um 90 Grad versetzte Sinus bzw. Cosinusschwingungen werden ausgewertet. Daraus wird bestimmt, in welche Richtung (im oder gegen Uhrzeigersinn) und wie weit (inkrementell) gedreht wurde. Mithilfe dieser Logik kann durch ein Menü eine Bewegungsstufe ausgewählt werden, die der Schrittmotor fahren soll.\cite{Basler.2016} Bei einer Drehung im Uhrzeigersinn wird im Menü eine Bewegungsstufe höher und bei einer Drehung gegen den Uhrzeigersinn eine Bewegungsstufe niedriger ausgewählt. Zusätzlich zum Drehwinkel-Encoder ist auch noch ein Schaltfunktion im Bauteil selbst integriert. Durch eindrücken des Encoders wird ein Taster betätigt, durch denn der eingestellte Wert bestätigt und an den Arduino zur weiteren Verarbeitung weitergegeben wird. Zur Besseren Handhabung des Drehwinkel-Encoders wurde noch ein Drehgriff angefertigt und auf dem Drehgeber montiert.
Weitere Details: 
\begin{itemize}
	\item \textbf{Abmessungen ($b \times l \times h$):} $18 \ mm \times 31 \ mm \times 30 \ mm$
	\item \textbf{Betriebsspannung:} 3,3 - 5\ V
	\cite{SimacElec.2019}
\end{itemize}

\section{Schrittmotorsteuerung}	

Für eine einfachere Bedienung des Schrittmotors wurde ein Schrittmotortreiber mit integriertem Übersetzer verbaut. Bei einer Leistung von bis zu 35\ V und ± 2\ A ist der DEBO DRV A4988 für den Betrieb von bipolaren Schrittmotoren ausgelegt. Auf dem Treiber ist ein Stromregler mit fester Ausschaltzeit integriert, bei dem zwischen einem langsamen und einem gemischten Abschaltmodus gewählt werden kann. Durch eine Impulseingabe wird der Motor um einen Mikroschritt angetrieben. Der Vorteil der Schrittmotorsteuerung liegt darin, dass keine Phasensequenztabellen, Hochfrequenz-Steuerleitungen oder komplexe Schnittstellen programmiert werden müssen. Im Schrittbetrieb wählt der A4988 automatisch den Abklingmodus, langsam oder gemischt. Im gemischten Modus wird im Abklingvorgang zwischen dem schnellen und langsamen Modus gewechselt. Dabei führt der gemischte Modus zu einer Verringerung der hörbaren Motorgeräusche, einer höheren Schrittgenauigkeit und einer geringeren Verlustleistung.  
Weitere Details: \begin{itemize}
	\item \textbf{Abmessungen ($b \times l \times h$):} $5 \ mm \times 5 \ mm \times 0,9 \ mm$
	\item \textbf{Steuerspannung:} 3,3 - 5\ V
	\item \textbf{Maximale Ausgangskapazität:} bis 35\ V und $\mp$ 2\ A
	\item \textbf{Schutzschaltungen:}  Thermische Abschaltschaltung, Schutz vor Masseschluss, Schutz vor kurzgeschlossener Last, Überkreuzungsstromschutz
\cite{Allegro.2022}
\end{itemize}

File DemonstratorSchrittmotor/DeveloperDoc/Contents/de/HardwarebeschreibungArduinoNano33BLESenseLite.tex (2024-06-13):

% !TeX spellcheck = de_DE/GB

\chapter{Hardwarebeschreibung des Arduino}
\begin{figure}[htb]
		\input{tikz/ArduinoNano33BLESense}
		\caption{Arduino Nano 33 BLE Sense (Vereinfachte Darstellung)} \label{ArduinoNano33BLESense1}
		\begin{tabularx}{\textwidth}{|p{1.5cm}|X|}
			\hline
			\textbf{Pos.Nr.} & \textbf{Modul/Sensor} \\
			\hline
			P1 & Mikrophone \\
			\hline
			P2 & 9-Achs-IMU \\
			\hline
			P3 & Näherungs-,Umgebungslicht-, Farb- und Gestensensor \\
			\hline
			P4 & Drucksensor \\
			\hline
			P5 & Bluetooth-Modul \\
			\hline
		\end{tabularx}
		\captionof{table}{Arduino Nano 33 BLE Sense \cite{Ard.2024}} \label{ArduinoNano33BLESense2}
\end{figure}
\section{Aufbau des Arduinos}
\cite{Ard.2024}
\\
Der Arduino Nano 33 Bluetooth Low Energie (BLE) Sense Lite ist ein Mikrocontroller basierend auf dem Nordic nRF52840-SoC (System-on-Chip). Trotz seiner kompakten Bauweise mit einer Größe von 45 x 18 mm verfügt es über mehrere verschiedene integrierte Sensoren, Aktoren und konnektive Schnittstellen (siehe \autoref{ArduinoNano33BLESense1}). Zudem hat der Arduino-Prozessor einen 1 MB Flash-Speicher und 256 KB RAM. Bei dem Prozessor handelt es sich um einen Arm\textregistered Cortex-M4F Prozessorkern, welcher mit einer Taktrate von 64 MHz arbeitet und für Mikrocontroller Anwendungen optimiert ist. Dieser bietet eine gute Leistung bei geringen Stromverbrauch und ist auch für Echtzeitverarbeitungsaufgaben geeignet. Außerdem besitzt der Prozessor eine Floating Point Unit (FPU), wodurch sich Datenverarbeitungsoperationen effizient verarbeiten lassen.Mithilfe einer integrierten Steckverbindung (engl. \glqq header \grqq) kann der Mikrocontroller direkt auf ein Board gesteckt werden. \cite{Arm.2020}

\section{Integrierte Sensorik}
Der Arduino Nano 33 BLE-Sense Lite verfügt über eine Vielzahl von integrierten Sensoren und Aktoren mit denen verschiedene Umwelteigenschaften detektiert werden können. Dazu gehören die in den folgenden Abschnitten beschriebenen Sensoren und Aktoren.
\subsection{9-Achs-IMU für die Bewegungserkennung (LSM9DS1)}
	Die Trägheitsmesseinheit LSM9DS1 ist ein System-in-Package, d.h. auf engsten Raum werden mehrere elektronische Komponenten oder Chips in einem Paket miteinander kombiniert.\cite{Lienig.2012} Die IMU verfügt über einen 3D-Linearbeschleunigungsmesser, ein 3D-Gyroskop und einen 3D-Magnetometer. Außerdem beinhaltet das System eine serielle I2C (Inter-Integrated-Circuit)-Bus Schnittstelle, die einen Standard und einen Fast Mode (100/400 kHz) bereitstellt, zudem eine serielle SPI-Standardschnittstelle. Der Sensor hat einen linearen Beschleunigungsmesser (Accelerometer) mit wählbarer Skala von ±2/±4/±8/±16 g, es misst die lineare Beschleunigung in drei Achsen (x, y, z) und ermöglicht die Erfassung von Änderungen der Geschwindigkeit und Position. Das Magnetfeld ist mit einer wählbaren Skala von ±4/±8/±12/±16 Gs ausgestattet, damit misst es das magnetische Feld in den drei Achsen und ermöglicht die Bestimmung der Ausrichtung relativ zur Erdmagnetfeldrichtung. Das 3D-Gyroskop ist mit wählbarem Skalenendwert: ±125/±250/±500/±1000/±2000 $\frac{Grad}{s}$ und ist dafür zuständig, die Winkelgeschwindigkeit bzw. Drehbewegung um die drei Achsen zu erfassen.\cite{STM1.2015}\cite{Ard.2024}
Mögliche Anwendungsbereiche sind zum Beispiel eine Bewegungssteuerungen (Drohnensteuerung, Robotik und industrielle Automatisierung), Schwingungsüberwachung und -kompensation, Antennen, Plattformen, optische Bild- und Objektivstabilisierung.  

\subsection{Näherungs-,Umgebungslicht-, Farb- und Gestensensor (APDS9960)}
	Hierbei handelt sich um einen sehr vielseitigen Sensor. Er dient zur Gestenerkennung, Farberkennung, Abstandsmessung und Umgebungslichtmessung. Die Gestenerkennung nutzt vier gerichtete Fotodioden, um reflektierte Infrarot-Energie (die von der integrierten LED stammt) zu erfassen, um die physischen Bewegungsinformationen (d.h. Geschwindigkeit, Richtung und Entfernung) in digitale Informationen zu übersetzen. Die Näherungserkennung ermöglicht die Messung der Entfernung durch die Erkennung der reflektierten Infrarot-Energie, (von der integrierten LED) mit Hilfe einer Fotodiode. Erkennungsereignisse sind interruptgesteuert und treten immer dann auf, wenn das Näherungsergebnis die oberen und/oder unteren Schwellenwerte überschreitet. Der Sensor verfügt zudem über Offset-Einstellregister, um den System-Offset zu kompensieren, der durch unerwünschte Infrarot-Energiereflexionen am Sensor entsteht. Die Infrarot-LED-Intensität ist werksseitig eingestellt, so dass eine Kalibrierung der Endgeräte aufgrund von Bauteilschwankungen nicht erforderlich ist. Die Farb- und Umgebungslichterkennung liefert Daten zur roten, grünen, blauen Farbspektrum und Daten zum klaren Lichtintensität. Jeder der Kanäle R, G, B, C hat einen UV- und Infrarot-Sperrfilter und einen speziellen Datenkonverter, der gleichzeitig 16-Bit-Daten erzeugt. Diese Architektur ermöglicht Anwendungen eine genaue Messung des Umgebungslichts zu messen und die Farbe zu erkennen, was es den Geräten wiederum ermöglicht, die Farbtemperatur zu berechnen und die Hintergrundbeleuchtung des Displays dementsprechend anzupassen.\cite{AT.2015}\cite{Ard.2024}
	
\subsection{Barometrischer Drucksensor (LPS22HB)}
	Der LPS22HB ist ein sehr kompakter Absolutdrucksensor, der auf dem piezoresistiven Prinzip basiert. Er fungiert als Barometer und verfügt über einen digitalen Ausgang. Zudem ist in diesem Drucksensor ein Temperatursensor integriert mit welchem Druckmessungen zusätzlich kompensiert werden können. Das Gerät besteht aus einem Sensorelement und einer Integrated-Circuit (IC)-Schnittstelle, die eine Kommunikation zwischen der Sensoreinheit und der Anwendung über Inter-Integrated Circuit (I2C) oder Serial Peripheral Interface (SPI) ermöglicht. Das Sensorelement erfasst den absoluten Druck und besteht aus einer speziell hergestellten, aufgehängten Membran. Der LPS22HB ist in einem vollständig vergossenem Land-Grid-Array-Gehäuse untergebracht, das kleine Löcher aufweist. Durch diese Öffnung gelangt der externe Druck auf das Sensorelement. Der Betrieb des Sensors ist über einen Temperaturbereich von -40 °C bis +85 °C gewährleistet. \cite{STM2.2017}\cite{Ard.2024}
	Anwendungsbereiche für diesen Sensor sind zum Beispiel: Wetterstationen, Höhenmesser, Luftdrucküberwachung in industriellen Prozessen oder tragbare smarte Geräte, wie Sportuhren oder Smartphones.
	
\subsection{Digitales Mikrophon (MP34DT05)}
Das MP34DT05-A ist ein kompaktes, stromsparendes, omnidirektionales, digitales
Mikrofon mit einem kapazitiven Sensorelement und einer IC-Schnittstelle.
Das Sensorelement, das in der Lage ist, akustische Wellen zu detektieren, wird mit
einem speziellen Silizium-Mikrobearbeitungsverfahren für die Herstellung von
Audiosensoren hergestellt. Die IC-Schnittstelle wird in einem speziellen Halbleiterherstellungsverfahren (CMOS-Verfahren) hergestellt, das die Entwicklung einer speziellen Schaltung ermöglicht, die ein digitales Signal im PDM (Pulsdichtenmodulation) -Format extern bereitstellen kann. Das Mikrofon hat einen Signal-Rausch-Abstand von 64 dB und eine Empfindlichkeit von -26 dBFS ±3 dB. Sein maximaler Schalldruckpegel liegt bei 122,5 dBSPL. Der MP34DT05-A ist in einem SMD-kompatiblen, EMI-geschirmten Top-Port-Gehäuse erhältlich und arbeitet zuverlässig über einen erweiterten Temperaturbereich von -40 °C bis +85 °C. Abmessungen des Gehäuses HCLGA-4 LD sind 3 x 4 x 1 (in mm). Anwendung findet das Modul Beispielsweise in mobilen Endgeräten, im Bereich der Spracherkennung sowie in Laptops und Notebooks.\cite{STM3.2021}\cite{Ard.2024}

\subsection{DC-DC-Wandler (MPM3610)}
Das MPM3610-Modul ist ein integriert Gleichspannungs- zu Gleichspannungs-Wandler. Dieser kann Eingangsspannungen von bis zu 21 V verarbeiten mit einem Wirkungsgrad von mindestens 65\% bei minimaler Last. Bei einer Eingangsspannung erhöht sich der Wirkungsgrad auf 85\%.\cite{Ard.2024}

\section{Beschreibung der Schnittstellen}
Der Arduino Nano 33 BLE-Sense Lite bietet eine Vielzahl von Schnittstellen, die das Board mit anderen Komponenten und Geräten einfach verbinden lassen. In diesem Abschnitt sind einige Details zu den wichtigsten Schnittstellen des Boards erläutert.
\begin{figure}
	\input{tikz/ArduinoPinout}
	\caption{Arduino Nano Pinbelegung \cite{Ard.2024}}
	\label{fig:arduinopinout}
\end{figure}

\subsection{I2C}
Der Inter-Intergrated-Circuit (I2C) -Bus ermöglicht die geräteinterne Kommunikation von Mikrocontrollern mit Sensoren, externen Bildschirmen, Echtzeituhren und vielen anderen Bausteinen. Das Kommunikationsprotokoll basiert auf dem Master-Slave-Prinzip. Der Master initiiert und beendet die Kommunikation, stellt den Takt zur Synchronisation bereit und löst Kommunikationsprobleme. Jeder Slave hat eine eindeutige Adresse, mit einer Länge von 7 Bit und ermöglicht die Adressierung von bis zu 112 Slaves. Geräte mit unterschiedlichen Adresslängen können im selben Bus koexistieren. Bevor der Master Daten überträgt oder empfängt, muss er einen Slave mit einer vorher vereinbarten Adresse ansprechen.\cite{Meroth.2018}\cite{STM1.2015}\cite{Bernstein.2020} Sind ihre Adressen in Übereinstimmung kann im nächsten Schritt ein einzelnes Bit gesendet werden, mit dem dann festgelegt wird, ob der Master Daten an dem Slave übertragen (Binär:1) oder auslesen möchte (Binär:0). Dieser Datenaustausch wird danach bestätigt, sodass weitere Daten ausgetauscht werden können. Zur Beendigung des Datenaustausches wird ein Stop-Signal gesendet.\cite{Gehrke.2022} In der minimalen Konfiguration werden Master und Slave über die bidirektionalen Busleitungen SDA und SCL verbunden, die über Pull-up-Widerstände an die Versorgungsspannung angeschlossen sind. Weitere Geräte können durch Verbindung ihrer SDA- und SCL-Anschlüsse mit den entsprechenden Busleitungen an den Bus angeschlossen werden.\cite{Meroth.2018} In diesem Projekt dient der Arduino als Master und ein zusätzlich angeschlossenes OLED-Bildschirm als Slave.

\subsection{USB:}
Das Board kann über einen Micro-Universal-Serial-Bus (Micro-USB) mit einem Computer verbunden werden, um es zu programmieren oder Daten zu übertragen. Die Datenübertragungsrate beträgt dabei 12 Mbit/s. Außerdem kann der Arduino über diesen USB-Port Strom beziehen.

\subsection{Bluetooth\textregistered 5}
Die Bluetooth-Verbindung kann als drahtloses Kommunikationsweg eingesetzt werden. Dieses Bluetooth-Protokoll hat eine Übertragungsrate von 2 Megabit pro Sekunde (Mbps) und eine Sendeleistung von +8 Dezibel Milliwatt (dBm). Die Empfindlichkeit beträgt dabei -95 dBm. Des weiteren verbraucht diese Verbindung im Sendebetrieb 4,8 mA und 4,6 mA im Empfangsbetrieb. Das Bluetooth Modul ist kompatibel mit mehreren Protokollen unter anderem mit dem \textit{Thread-Protokoll} und dem \textit{Zigbee-Protokoll}.\cite{Ard.2024} \cite{NrdSem4.2024}

\subsection{Weitere Kommunikationsschnittstellen}
\cite{Ard.2024}
\begin{itemize}
	\item \textbf{NFC-A-Tag:} Near Field Communication (NFC) ist eine zusätzliche Funktion zur drahtlosen Kommunikation über kurze Distanzen. Zudem besitzt der NFC-A-Tag die Funktionen sich in einen Bereitschaftsmodus versetzen zu lassen, dass durch ein NFC-fähiges Gerät dann initiiert werden kann. Außerdem unterstützt es \textit{touch-to-pair}, diese Funktion ermöglicht eine Kopplung mit anderen NFC-fähigen Geräten durch Berührung.
	\item \textbf{Arm CryptoCell CC310 Security Subsystem:} Für die Durchführung kryptografischer Operationen und Sicherheitsaufgaben.\\ \cite{NrdSem.2024}
	\item \textbf{QSPI/SPI/TWI/$I^2$S/PDM/QDEC:} Verschiedene weitere serielle Kommunikationsschnittstellen, die für den Datenaustausch verwendet werden können.
	\item \textbf{EasyDMA:} Direkt Memory Access (DMA) ist für die Übertragung von Daten zwischen verschiedenen Speicherbereichen, ohne dabei die CPU zu belasten.\cite{Gehrke.2022}
	\item \textbf{Analog-Digital-Wandler (ADC):} Wandelt analoge Eingangsignale in digitale Daten um. Der Wandler hat eine Auflösung von 12 Bit und eine maximale Abtastrate von 200 Kilosamples pro Sekunde (ksps).
	\item \textbf{128-Bit-AES/ECB/CCM/AAR-Co-Prozessor:} Co-Prozessor für kryptografische Operationen, der auf dem Advanced Encryption Standard (AES) basiert. Dieser unterstützt verschiedene Betriebsmodi wie Electronic Codebook (ECB), Counter with CBC-MAC (CCM) und Automatic Address Recognition (AAR). \cite{NrdSem2.2024}
	\item \textbf{Quad-SPI-Schnittstelle 32 MHz:} SPI-Schnittstelle, die eine maximale Taktrate von 32 MHz unterstützt. Quad-SPI ermöglicht es, Daten schneller als die herkömmliches SPI zu übertragen, indem es vier Datenleitungen verwendet.\cite{NrdSem3.2023}
\end{itemize}

\subsection{Digitale Ein- und Ausgangspins}
Das Board verfügt über 14 digitale Ein- und Ausgangspins. Die digitalen Pins können nur zwei Zustände, nach dem Binär-System lesen: wenn ein Spannungssignal vorliegt und wenn kein Signal vorhanden ist (0 oder 1). Einige der Pins sind zudem zur Pulsweitenmodulation fähig (D3, D5, D6, D9, D10). Außerdem sind die digitalen Pins D11 und D12 als Master-Output-Slave-Input (MOSI) und als Master-Input-Slave-Output (MISO), in einer Serial-Peripheral-Interface (SPI) Kommunikation einsetzbar.\cite{Ard.2024}

\subsection{Analoge Eingangspins}
Die Platine hat zusätzlich 8 analoge Eingangspins (A0-A7) die wiederum als Analog-Digital-Wandler (ADC) verwendet werden können. Außerdem sind diese Pins als digitale Ein-/Ausgangspins konfigurierbar. Der Pin A0 kann zudem als Digital-Analog-Wandler (DAC) konfiguriert werden. Die beiden Pins A4 und A5 können außerdem für die I2C-Kommunikation verwendet werden. Dabei fungiert A4 als Datenleitung (SDA), während A5 als Taktleitung (SCL) fungiert.\cite{Ard.2024}

\subsection{Weitere Pins}
\begin{itemize}
	\item \textbf{+3,3 V}: Erzeugt interne Stromquelle im Gerät und wird als Referenzspannung verwendet.
	\item \textbf{VIN}: Stromversorgung
	\item \textbf{5V}: Gibt 5V an die externen Komponenten ab. 
	\item \textbf{RST-Pin}: Dient zum Zurücksetzen des Arduinos.
	\item \textbf{AREF-Pin}: Liefert die Spannungsreferenz, die der Mikrocontroller zur Zeit verwendet.
	\\ \cite{Ard.2024}
\end{itemize}

\subsection{LED-Lampen}
Im Arduino selbst sind 3 LED´s verbaut, die auch alle programmiert werden können. Diese sind vor allem für die Überprüfung der Sensorik oder Softwareprogrammen nützlich. Zu den LED-Lampen gehören: 
\begin{itemize}
	\item Programmierbare Power-LED (grün): Zeigt an, dass das Arduino-Board eingeschaltet ist.
	\item Programmierbare LED (orange)
	\item Programmierbare RGB-LED
	\\ \cite{Ard.2024}
\end{itemize}

\section{Hinweis Arduino 33 BLE Sense Lite \label{Hinweis Arduino 33 BLE Sense Lite}}
Der Arduino Nano 33 BLE Sense \underline{Lite} ist eine komprimierte Variante vom ursprünglichen Arduino Nano 33 BLE Sense, welcher zusätzlich noch über einen Temperatur- und Feuchtigkeitssensor verfügt. Der Lite hat stattdessen einen Drucksensor integriert, über welchem auch die Temperatur gemessen werden kann, jedoch nicht die Feuchtigkeit.\cite{PetrFilipi.2022}
\section{Bezugsquellen}
Als Bezugsquellen dienten vor allem Datenblätter der Hersteller. Die meisten Informationen konnten dem Datenblatt des Arduino entnommen werden, jedoch ist dazu anzumerken, dass sich dieses Datenblatt auf das Arduino 33 BLE Sense bezieht und nicht auf das Arduino 33 BLE Sense \emph{Lite}. Speziell zum \emph{Lite} gibt es jedoch kein Datenblatt, so wurde das Datenblatt vom Arduino 33 BLE Sense herangezogen. Dies stellt sonst kein Problem dar, da sich, wie in \ref{Hinweis Arduino 33 BLE Sense Lite} beschrieben, nur um eine komprimierte Version des Arduino 33 BLE Sense handelt.

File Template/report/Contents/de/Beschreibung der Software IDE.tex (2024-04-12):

% !TeX spellcheck = de_DE/GB

\chapter{Beschreibung der Software IDE}

\section{Installation der Arduino IDE}
Um Mikrocontroller von Arduino, wie den verwendeten Arduino Nano 33 BLE Sense Lite, programmieren zu können, wird die Software namens „Arduino IDE“ in der Version 2.3.2 verwendet. 
Alternativ dazu könnten auch andere Entwicklungsumgebungen, wie Qt verwendet werden, die eine Programmierung in der Programmiersprache C++ ermöglicht. \\
Vorteil der Arduino IDE sind vor allem ihre Funktionen, die das Einbinden der Software auf dem Mikrocontroller vereinfachen.\\
Der Bezug der Software Arduino IDE erfolgt über die offizielle Webseite von Arduino, welche unter www.arduino.cc/software erreichbar ist. Auf dieser Plattform stehen diverse Versionen, für unterschiedliche Betriebssysteme, wie Windows, Linux und Mac OS X, sowie in verschiedenen Dateiformaten, zur Auswahl bereit. Um die Anwendung zu installieren, muss die heruntergeladene Datei ausgeführt und den Installationsanweisungen gefolgt werden. Danach ist die korrekte Konfiguration des verwendeten Entwicklungsboards sowie die Installation entsprechender Bibliotheken erforderlich.\\

\section{Beschreibung der Entwicklungsumgebung}
Nach dem Start der installierten Anwendung öffnet sich die Hauptoberfläche.
\begin{figure}[htb]
	\begin{center}
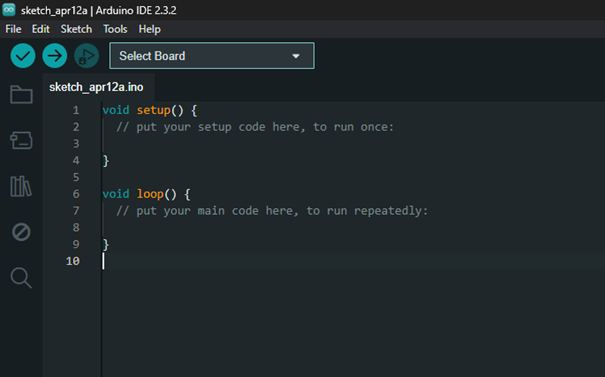
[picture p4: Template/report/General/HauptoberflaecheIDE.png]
		
		\caption{Hauptoberfläche in der Arduino IDE} \label{Hauptoberfläche in der Arduino IDE}
	\end{center}
\end{figure}
Oben in der Hauptoberfläche befindet sich eine Menüleiste, die verschiedene Menüs wie "Datei", "Bearbeiten" und "Sketch" enthält. Diese Menüs ermöglichen das Bearbeiten und Öffnen von Sketches, also Programmen in der IDE, das Kompilieren und Hochladen von Code sowie das Verwalten von Bibliotheken. Außerdem bietet die Menüleiste ein Hilfe-Menü, das bei Fragen und Problemen hilfreich ist. \\
Die Symbolleiste auf der linken Seite der Hauptoberfläche bietet Schaltflächen für häufig genutzte Funktionen wie das Verwalten von Sketches, Boards und Bibliotheken.\\
Im Zentrum der Hauptoberfläche befindet sich ein Code-Editor, der die Bearbeitung der Sketches ermöglicht. Direkt darunter erscheint nach dem ersten Kompilieren eines Sketches ein Ausgabefenster, das den Kompilierungs- und Hochladeprozess sowie eventuelle Fehler während der Kompilierung anzeigt. Dadurch können Probleme im Code schnell identifiziert werden.\\

\section{Erste Schritte in der Entwicklungsumgebung}
\subsection{Auswahl des Mikrocontrollers}
In der Entwicklungsumgebung können sofort Sketche geöffnet und geschrieben werden. Dafür wird zunächst noch kein Mikrocontroller benötigt. Um den Sketch aber kompilieren zu können, muss das korrekte Board ausgewählt werden.
Dafür muss zunächst das passende Board installiert werden. \\
 Dies erfolgt über den „Boards-Manager“.
\begin{figure}[htb]
	\begin{center}
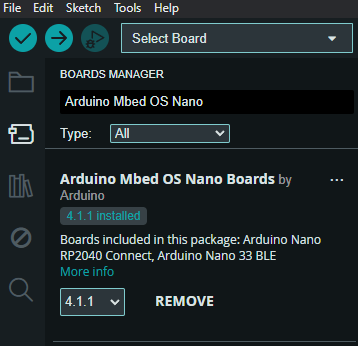
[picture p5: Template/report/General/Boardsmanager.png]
		
		\caption{Installation des Boards} \label{Installation des Boards}
	\end{center}
\end{figure}
Dort kann in diesem Fall die Datei „Arduino Mbed OS Nano“ in der aktuellen Version 4.1.1 heruntergeladen und installiert werden. Danach kann unter „Select Board“ das Board „Arduino BLE Sense 33“ ausgewählt werden.\\
Alternativ kann man das Board über ein USB-Kabel angeschlossen werden, sollte man den Mikrocontroller bereits zur Hand haben. Unter „Select Board“ sollten nun bereits das korrekte Board und der entsprechende COM, also in diesem Fall der USB-Port, angeboten werden. Wählt man diese nun aus, muss man dann nur noch den Installationsanweisungen folgen, um das Board zu installieren.\\

\subsection{Bibliotheken einbinden}
Von Arduino gibt es bereits sehr viele offiziell unterstützte Bibliotheken. Will man diese in einem Sketch nutzen, muss man diese zunächst installieren.
Dafür kann man über den „Library Manager“ die nötige Bibliothek herunterladen und installieren. Die Suchfunktion hilft dabei, die korrekte Bibliothek zu finden.
\begin{figure}[htb]
	\begin{center}
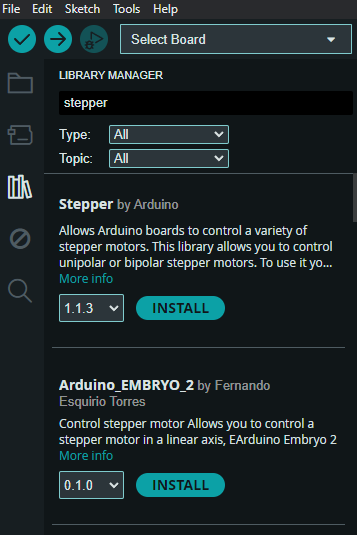
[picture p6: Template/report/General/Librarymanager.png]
		
		\caption{Herunterladen von Bibliotheken} \label{Herunterladen von Bibliotheken}
	\end{center}
\end{figure}
Nachdem die Bibliothek installiert ist, kann sie im „header“ in den Sketch eingebunden werden.\\
Möchte man eine Bibliothek nutzen, die nicht im „Library Manager“ zu finden ist, kann diese über „Sketch->Include Libraries->Add .ZIP Library…“ eingebunden werden.

\section{Programmierung}
Wird ein neuer Sketch geöffnet, sind bereits die Funktionen „void setup()“ und „void loop“ hinterlegt.

\subsection{header}
Im „header“ werden vor allem alle nötigen Bibliotheken hinterlegt und initialisiert. Gleichzeitig können hier aber auch Adressen von Peripheriegeräten hinterlegt erste wichtige Variablen definiert.

\subsection{void setup()}
Die „void setup()“-Funktion wird jedes Mal einmal ausgeführt, wenn der Arduino an den Strom angeschlossen wird, oder der Reset-Knopf gedrückt wird.
Hier wird zum Beispiel die serielle Kommunikation gestartet, aber auch verwendete Pins initialisiert und zugewiesen.

\subsection{void loop()}
In der „void loop()“-Funktion findet der größte Teil des Programmes statt. Der Inhalt dieser Funktion wird dauerhaft wiederholt, bis entweder kein Strom mehr an dem Arduino anliegt, oder der Reset-Knopf gedrückt wird und somit zunächst erst die „void setup()“-Funktion wieder gestartet wird.

\section{"hello world"}
Um die Funktion eines Systems zu testen, wird oft zunächst ein sehr simples Programm oder eine sehr grundlegende Funktion getestet.\\
In diesem Fall kann hier über Datei -> Beispiele -> 01.Basics -> Blink ein Sketch geöffnet werden, in dem die auf dem Arduino Nano 33 BLE Sense Lite aufgebrachte LED in einem fest gelegten Takt blinkt, wodurch die korrekte Auswahl des Boards und die Übertragung des Sketches auf den Mikrocontroller getestet werden können. \\

%void setup() {
%	// initialize digital pin LED_BUILTIN as an output.
%	pinMode(LED_BUILTIN, OUTPUT);
%}
%
%void loop() {
%	digitalWrite(LED_BUILTIN, HIGH);  // turn the LED on (HIGH is the voltage level)
%	delay(1000);                      // wait for a second
%	digitalWrite(LED_BUILTIN, LOW);   // turn the LED off by making the voltage LOW
%	delay(1000);                      // wait for a second
%}

In der „void setup()“-Funktion wird in diesem Beispiel zunächst über den Ausdruck "pinMode(LED_BUILTIN, OUTPUT)" die auf dem Mikrocontroller verbaute LED in dem Sketch aufgerufen und eingebunden.\\
In „void loop()“ wird durch den Befehl „digitalWrite()“ zunächst die LED eingeschaltet, indem eine Spannung an sie angelegt wird, dann nach einer kurzen Verzögerung durch den gleichen Befehl wieder ausgeschaltet, indem die anliegende Spannung gesenkt wird. Die Verzögerung kann mit dem „delay()“-Befehl eingestellt werden, indem der Wert in der Klammer angepasst wird. Dabei wird der Wert in Millisekunden angegeben.

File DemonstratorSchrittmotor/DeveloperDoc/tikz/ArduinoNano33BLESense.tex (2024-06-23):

%%%%%%
%
% $Autor: ter Veen $
% $Datum: 01.06.2024 $
% $Version: 1 $
% $Pfad: SchrittmotorArduino/DevoloperDoc/tikz/ArduinoPinout.tex $
%
%%%%%%

% Für schnelle Anpassungen
%\documentclass[12pt,a4paper]{scrbook}
%\usepackage{tikz}
%\usetikzlibrary{shapes,arrows.meta,positioning}
%\begin{document}
	\begin{tikzpicture}[scale=0.8]
		% Arduino Dummy
		\draw[fill=blue!20] (1,0) rectangle (15,5);
	
		% Module
		\draw[fill=gray!30] (10.8,1) rectangle (14,4) node[pos=0.5, align=center] {P5};
		\draw[fill=green!30] (14,1) rectangle (15,4) node[pos=0.5, align=center] {};
		\draw[fill=gray!30] (0.5,1.3) rectangle (2.5,3.7) node[pos=0.5, align=center] {USB};
		\draw[fill=gray!30] (9.5,1.9) rectangle (10.7,3) node[pos=0.5, align=center] {P1}; % Mikrophone
		\draw[fill=gray!30] (8,3.1) rectangle (9.2,4.1) node[pos=0.5, align=center] {P2}; % IMU
		\draw[fill=gray!30] (8,2.1) rectangle (9.4,3) node[pos=0.5, align=center] {P3}; %  Näherungs-,Umgebungslicht-, Farb- und Gestensensor
		\draw[fill=gray!30] (8.9,0.7) rectangle (9.5,1.3) node[pos=0.5, align=center] {P4}; % Drucksensor
		\draw[fill=gray!30] (4.4,1.8) rectangle (5.4,3.1) node[pos=0.5, align=center] {};
		\draw[fill=gray!20] (4.9,2.45) circle (0.25) node[pos=0.5, align=center] {};
		
		% Bohrlöcher
		\draw[fill=white] (1.3,0.3) circle (0.2) node[right=1mm]{};
		\draw[fill=white] (1.3,4.7) circle (0.2) node[right=1mm]{};
		\draw[fill=white] (14.7,0.3) circle (0.2) node[right=1mm]{};
		\draw[fill=white] (14.7,4.7) circle (0.2) node[right=1mm]{};
		
		% LED´s
		\draw[fill=green] (1.5,4) circle (0.25) node[right=3mm] {Power-LED};
		\draw[fill=orange] (1.5,1) circle (0.25) node[right=3mm] {RGB-LED};
		\draw[fill=blue!40] (10.3,3.6) circle (0.25) node[above=4mm] {RGB-LED};
		
	\end{tikzpicture}
%\end{document}

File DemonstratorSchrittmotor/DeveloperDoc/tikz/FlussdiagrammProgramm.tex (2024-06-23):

%%%%%%%%%%%%%%%%%%%%
%
% $Beschreibung: Flussdiagramm des Schrittmotors $
% $Autor: Hanneken $
% $Datum: 15.06.2024 $
% $Pfad: DemonstratorSchrittmotor/DeveloperDoc/tikz/FlussdiagrammProgramm $
% $Version: 1 $
%
%
%%%%%%%%%%%%%%%%%%%

\resizebox{\textwidth}{!}{%
	\begin{tikzpicture}[
		node distance=0.8cm and 1.5cm,
		startstop/.style={circle, draw, minimum size=1cm},
		process/.style={rectangle, draw, text width=2.7cm, align=center},
		decision/.style={diamond, draw, text width=2cm, align=center},
		arrow/.style={->, thick}
		]
		
		% Nodes
		\node (start) [startstop] {Start};
		\node (init) [process, below=of start] {Initialisierung};
		\node (display) [process, below=of init] {Display-Start};
		\node (status) [process, below=of display] {Status: Bereit};
		\node (wait) [process, below=of status] {Warten auf Eingabe};
		\node (enc_turned) [decision, below=of wait] {Encoder gedreht?};
		\node (button_pressed) [decision, right=of enc_turned, xshift=1.5cm] {Taster gedrückt?};
		\node (enc_left) [process, below left=of enc_turned, xshift=1cm] {Encoder links};
		\node (enc_right) [process, below right=of enc_turned, xshift=-1cm] {Encoder rechts};
		\node (stage_gt1) [decision, below=of enc_left] {Stufe > 1};
		\node (stage_lt10) [decision, below=of enc_right] {Stufe < 10};
		\node (stage_dec) [process, below=of stage_gt1] {Stufe -1};
		\node (stage_inc) [process, below=of stage_lt10] {Stufe +1};
		\node (update1) [process, below=of stage_dec] {Display aktualisiert};
		\node (update2) [process, below=of stage_inc] {Display aktualisiert};
		\node (ref_run) [process, below right=of button_pressed, xshift=-1cm] {Referenzfahrt};
		\node (end_pressed) [decision, below=of ref_run] {Endschalter?};
		\node (demo_run) [process, below=of end_pressed] {Demonstrations- fahrt};
		\node (display_run) [process, below=of demo_run] {Display: wird ausgeführt};
		\node (shuttle_move) [process, below=of display_run] {Schlitten pendelt};
		\node (display_ready) [process, below=of shuttle_move] {Display: Startbereit};
		
		% Arrows
		\draw [arrow] (start) -- (init);
		\draw [arrow] (init) -- (display);
		\draw [arrow] (display) -- (status);
		\draw [arrow] (status) -- (wait);
		\draw [arrow] (wait.south) -- ++(0,-0.5) -| (enc_turned.north);
		\draw [arrow] (wait.south) -- ++(0,-0.5) -| (button_pressed.north);
		\draw [arrow] (enc_turned) -- (enc_left);
		\draw [arrow] (enc_turned) -- (enc_right);
		\draw [arrow] (enc_left) -- (stage_gt1);
		\draw [arrow] (enc_right) -- (stage_lt10);
		\draw [arrow] (stage_gt1) -- (stage_dec);
		\draw [arrow] (stage_lt10) -- (stage_inc);
		\draw [arrow] (stage_dec) -- (update1);
		\draw [arrow] (stage_inc) -- (update2);
		\draw [arrow] (update1.south) -- ++(0,-0.5) -| ++(-5,0) |- (wait.west);
		\draw [arrow] (update2.south) -- ++(0,-0.5) -| ++(-8,0) |- (wait.west);
		\draw [arrow] (button_pressed) -- (ref_run);
		\draw [arrow] (ref_run) -- (end_pressed);
		\draw [arrow] (end_pressed) -- (demo_run);
		\draw [arrow] (demo_run) -- (display_run);
		\draw [arrow] (display_run) -- (shuttle_move);
		\draw [arrow] (shuttle_move) -- (display_ready);
		\draw [arrow] (display_ready.east) -- ++(1.5,0) |- (wait.east);
	\end{tikzpicture}
} % end resizebox

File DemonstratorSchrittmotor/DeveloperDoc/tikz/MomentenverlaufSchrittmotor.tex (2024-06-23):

%%%%%%%%%%%%%%%%%%%%
%
% $Beschreibung: Momentenverlauf für den NEMA 17 $
% $Autor: Grönke $
% $Datum: 20.06.2024 $
% $Pfad: DemonstratorSchrittmotor/DeveloperDoc/tikz/MomentenverlaufSchrittmotor.tex $
% $Version: 1 $
%
%
%%%%%%%%%%%%%%%%%%%

	\begin{tikzpicture}
	\begin{axis}[
		width=10cm,
		height=6cm,
		xlabel={SPEED (PPS)},
		ylabel={TORQUE (kg·cm)},
		xmin=0, xmax=4000,
		ymin=0, ymax=1.6,
		xtick={0,500,1000,1500,2000,2500,3000,3500,4000},
		ytick={0,0.2,0.4,0.6,0.8,1,1.2,1.4,1.6},
		legend pos=north east,
		grid=both,
		major grid style={line width=.2pt,draw=gray!50},
		minor grid style={line width=.1pt,draw=gray!20},
		]
		\addplot[
		color=purple,
		line width=1pt
		]
		coordinates {
			(0,0.7)
			(500,0.82)
			(1000,0.82)
			(1500,0.8)
			(2000,0.78)
			(2500,0.75)
			(3000,0.73)
			(3500,0.7)
			(4000,0.68)
		};
	\end{axis}
\end{tikzpicture}

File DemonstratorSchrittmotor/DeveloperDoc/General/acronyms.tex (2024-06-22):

%%%%%%%%%%%%%%%%%%%%%%%%%%%%%%
%
% $Autor: Wings, Reck $
% $Datum: 2020-10-12 $
% $Pfad: DemonstratorSchrittmotor\DeleoperDoc\General\acronyms.tex $
% $Version: 1 $
%
%
%%%%%%%%%%%%%%%%%%%%%%%%%%%%%%

% Automatisches erstellen und referenzieren eines Abkürzungsverzeichnisses
%\usepackage[tooltip]{acro}
\usepackage{acro}
%\usepackage{acronym} nicht in Verwendung; hier erwähnt, weil immer Verwechslungen auftreten.

%\acsetup{
%%    list-type    = table ,
%    list-name    = Akronyme,
%    list-style   = longtable ,
%    list-heading = chapter*, % Kapitel ohne Nummerierung
%%    list-table-width = \textwidth-4\tabcolsep-6em,
%%    page-ref = dotfill , % <<< neue Instanz verwenden
%    list-short-format ={\bfseries}, % Abkürzungen in fetter Serifenschrift im Verzeichnis
%    first-long-format = {\itshape}, % Erste Lange Ausführung der Abkürzung kursiv gestellt
%}

% muss für Akronyme \ac statt see verwendet werden.
%\newcommand{\Siehe}{
%	\ifdefined\isGerman
%	\emph{siehe}
%	\else
%	\ifdefined\isEnglish
%	\emph{see}
%	\else
%	\emph{siehe}
%	\fi
%	\fi
%}

%%%%%%%%%%%%%%%%%%%%%%%%%%%%%%%%%%%%%%%%%%%%%%%%%%%%%
% A
%%%%%%%%%%%%%%%%%%%%%%%%%%%%%%%%%%%%%%%%%%%%%%%%%%%%%
\DeclareAcronym{aar}{
	short = AAR\index{AAR}, 
	long  = Automatic Address Recognition\index{Automatic Address Recognition!\Siehe AAR},
}

\DeclareAcronym{adc}{
	short = ADC\index{ADC}, 
	long  = Analog to Digital Converter\index{Analog to Digital Converter!\Siehe ADC},
}

\DeclareAcronym{aes}{
	short = AES\index{AES}, 
	long  = Advanced Encryption Standard\index{Advanced Encryption Standard!\Siehe AES},
}
\DeclareAcronym{ap}{
	short = AP\index{AP}, 
	long  = Average Precision\index{Average Precision!\Siehe {AP}},
}

\DeclareAcronym{api}{
    short = API\index{API}, 
    long  = Application Programming Interface\index{Application Programming Interface!\Siehe {API}},
}

\DeclareAcronym{ARM}{
	short = ARM\index{ARM}, 
	long  = Advanced RISC Machine\index{Advanced RISC Machine!\Siehe ARM},
}

%%%%%%%%%%%%%%%%%%%%%%%%%%%%%%%%%%%%%%%%%%%%%%%%%%%%%
% B
%%%%%%%%%%%%%%%%%%%%%%%%%%%%%%%%%%%%%%%%%%%%%%%%%%%%%

\DeclareAcronym{bs}{
    short = BS\index{BS}, 
    long  = Batch-Size\index{Batch-Size!\Siehe {BS}},
}

\DeclareAcronym{ble}{
	short = BLE\index{BLE}, 
	long  = Bluetooth Low Energie\index{Bluetooth Low Energie!\Siehe {BLE}},
}

%%%%%%%%%%%%%%%%%%%%%%%%%%%%%%%%%%%%%%%%%%%%%%%%%%%%%
% C
%%%%%%%%%%%%%%%%%%%%%%%%%%%%%%%%%%%%%%%%%%%%%%%%%%%%%

\DeclareAcronym{cad}{
	short = CAD\index{CCI},
	long  = Computer Aided Design\index{Computer Aided Design!\Siehe {CCI}},
}

\DeclareAcronym{cci}{
    short = CCI\index{CCI},
    long  = Camera Control Interface\index{Camera Control Interface!\Siehe {CCI}},
}

\DeclareAcronym{ccm}{
	short = CCM\index{CCM},
	long  = Counter with CBC-MAC\index{Counter with CBC-MAC!\Siehe{CCM}},
}

\DeclareAcronym{cli}{
	short = CLI\index{CLI},
%	long  = \TRANS{Kommandozeilenschnitte}{Command Line Interface}\index{\TRANS{Kommandozeilenschnitte}{Command Line Interface}!\Siehe {CCI}},
	long  = Command Line Interface\index{Command Line Interface!\Siehe {CCI}},
}

\DeclareAcronym{csi}{
  short = CSI\index{CSI},
  long  = Camera Serial Interface\index{Camera Serial Interface!\Siehe {CSI}},
}
  
\DeclareAcronym{cg}{
    short = Cg, 
    long = C for graphics,
}

\DeclareAcronym{cifar}{
    short = CIFAR\index{Datensatz!CIFAR} ,
    long  = Canadian Institute For Advanced Research\index{Canadian Institute For Advanced Research!\Siehe {CIFAR!\Siehe {Datensatz}}},
}

\DeclareAcronym{cnc}{
	short = CNC\index{CNN} ,
	long  = Computerized Numerical Control\index{Computerized Numerical Control!\Siehe {CNN}} ,
}

\DeclareAcronym{cnn}{
    short = CNN\index{CNN} ,
    long  = Convolutional Neural Network\index{Convolutional Neural Network!\Siehe {CNN}} ,
}

\DeclareAcronym{coco}{
  short = COCO\index{COCO},
  long  = Common Objects in Context\index{Common Objects in Context!\Siehe {COCO}}
}

\DeclareAcronym{cpu}{
    short = CPU\index{CPU} ,
    long  = Central Processing Unit\index{Central Processing Unit!\Siehe {CPU}} ,
}

\DeclareAcronym{csp}{
	short = CSP\index{CSP} ,
	long  = Cross Stage Partial Network\index{Cross Stage Partial Network!\Siehe {CSP}} ,
}

\DeclareAcronym{cuda}{
    short = CUDA\index{CUDA} ,
	long  = Compute Unified Device Architecture\index{Compute Unified Device Architecture!\Siehe {CUDA}} ,
}

\DeclareAcronym{cudnn}{
	short = cuDNN\index{cuDNN} ,
	long  = NVIDIA CUDA Deep Neural Network Library\index{NVIDIA CUDA Deep Neural Network Library!\Siehe {cuDNN}} ,
}

%%%%%%%%%%%%%%%%%%%%%%%%%%%%%%%%%%%%%%%%%%%%%%%%%%%%%
% D
%%%%%%%%%%%%%%%%%%%%%%%%%%%%%%%%%%%%%%%%%%%%%%%%%%%%%

\DeclareAcronym{dac}{
	short = DAC\index{DAC}, 
	long  = Digital to Analog Converter\index{Digital to Analog Converter!\Siehe DAC},
}

\DeclareAcronym{dll}{
    short = DLL ,
    long  = Dynamic Link Library,
    long-plural-form = Dynamic Link Libraries,
}

\DeclareAcronym{dma}{
	short = DMA\index{DMA}, 
	long  = Direkt Memory Access\index{Direkt Memory Access!\Siehe DMA},
}

\DeclareAcronym{dnn}{
    short = DNN ,
    long  = Deep Neural Network ,
}

%%%%%%%%%%%%%%%%%%%%%%%%%%%%%%%%%%%%%%%%%%%%%%%%%%%%%
% E
%%%%%%%%%%%%%%%%%%%%%%%%%%%%%%%%%%%%%%%%%%%%%%%%%%%%%
\DeclareAcronym{ecb}{
	short = ECB ,
	long  = Electronic Codebook ,
}

\DeclareAcronym{emi}{
	short = EMI ,
	long  = Electromagnetic Interference ,
}

%%%%%%%%%%%%%%%%%%%%%%%%%%%%%%%%%%%%%%%%%%%%%%%%%%%%%
% F
%%%%%%%%%%%%%%%%%%%%%%%%%%%%%%%%%%%%%%%%%%%%%%%%%%%%%

\DeclareAcronym{fp32}{
    short = FP32, 
    long  = Floating Point 32-bit,
}

\DeclareAcronym{flops}{
    short = Flops, 
    long  = Floating Point Operations per Second - Gleitkomma­operationen pro Sekunde,
}

\DeclareAcronym{fp16}{
    short = FP16, 
    long = Floating Point 16-bit,
}

\DeclareAcronym{fpga}{
  short = FPGA,
  long  = Field-Programmable Gate Array,
}

\DeclareAcronym{fps}{
    short = fps,
    long  = frames per second,
}

\DeclareAcronym{fpu}{
	short = FPU,
	long  = Floating Point Unit,
}

%%%%%%%%%%%%%%%%%%%%%%%%%%%%%%%%%%%%%%%%%%%%%%%%%%%%%
% G
%%%%%%%%%%%%%%%%%%%%%%%%%%%%%%%%%%%%%%%%%%%%%%%%%%%%%

\DeclareAcronym{gpio}{
  short = GPIO\index{GPIO},
  long  = General Purpose Input Output\index{General Purpose Input Output!\Siehe GPIO},
}

\DeclareAcronym{gpgpu}{
    short = GPGPU ,
    long  = General Purpose Computation on Graphics Processing Unit\index{General Purpose Computation on Graphics Processing Unit!\Siehe GPGPU} ,
}

\DeclareAcronym{gpu}{
    short = GPU\index{GPU} ,
    long  = Graphics Processing Unit\index{Graphics Processing Unit!\Siehe GPU} ,
}

%%%%%%%%%%%%%%%%%%%%%%%%%%%%%%%%%%%%%%%%%%%%%%%%%%%%%
% H
%%%%%%%%%%%%%%%%%%%%%%%%%%%%%%%%%%%%%%%%%%%%%%%%%%%%%

\DeclareAcronym{hdmi}{
  short = HDMI\index{HDMI},
  long  = High Definition Multimedia Interface\index{High Definition Multimedia Interface!\Siehe {HDMI}},
}

\DeclareAcronym{hy}{
	short = hy\index{HDMI},
	long  = Hybrid\index{Hybrid!\Siehe {HDMI}},
}

%%%%%%%%%%%%%%%%%%%%%%%%%%%%%%%%%%%%%%%%%%%%%%%%%%%%%
% I
%%%%%%%%%%%%%%%%%%%%%%%%%%%%%%%%%%%%%%%%%%%%%%%%%%%%%
\DeclareAcronym{ic}{
	short = IC\index{IC},
	long  = Inter Circuit\index{Inter Circuit!\Siehe IC},
}

\DeclareAcronym{i2c}{
    short = I\textsuperscript{2}C\index{I\textsuperscript{2}C},
    long  = Inter-Integrated Circuit\index{Inter-Integrated Circuit!\Siehe I\textsuperscript{2}C},
}    

\DeclareAcronym{i2s}{
    short = I\textsuperscript{2}S\index{I\textsuperscript{2}S},
    long  = Inter-IC Sound\index{Inter-IC Sound!\Siehe I\textsuperscript{2}S},
}    

\DeclareAcronym{ide}{
	short = IDE\index{IDE} ,
	long  = Integrated Development Environment\index{Integrated Development Environment!\Siehe IDE},
}

\DeclareAcronym{imu}{
    short = IMU\index{IMU} ,
    long  = \TRANS{Inertialmesseinheit}{Inertial Measurement Unit}\index{\TRANS{Inertialmesseinheit}{Inertial Measurement Unit}!\Siehe IMU},
}

\DeclareAcronym{int8}{
    short = INT8, 
    long = Integer 8-bit,
}

\DeclareAcronym{iot}{
    short = IoT ,
    long  = Internet of Things,
}

%%%%%%%%%%%%%%%%%%%%%%%%%%%%%%%%%%%%%%%%%%%%%%%%%%%%%
% J
%%%%%%%%%%%%%%%%%%%%%%%%%%%%%%%%%%%%%%%%%%%%%%%%%%%%%

%%%%%%%%%%%%%%%%%%%%%%%%%%%%%%%%%%%%%%%%%%%%%%%%%%%%%
% K
%%%%%%%%%%%%%%%%%%%%%%%%%%%%%%%%%%%%%%%%%%%%%%%%%%%%%

\DeclareAcronym{kdd}{
    short = KDD\index{KDD} ,
    long  = Knowledge Discovery in Databases\index{Knowledge Discovery in Databases!\Siehe KDD},
}

\DeclareAcronym{ki}{
    short = KI, 
    long  = Künstliche Intelligenz,
}

\DeclareAcronym{knn}{
    short = KNN, 
    long  = Künstliches Neuronales Netz,
}

%%%%%%%%%%%%%%%%%%%%%%%%%%%%%%%%%%%%%%%%%%%%%%%%%%%%%
% L
%%%%%%%%%%%%%%%%%%%%%%%%%%%%%%%%%%%%%%%%%%%%%%%%%%%%%

\DeclareAcronym{led}{
    short = LED\index{LED}, 
    long  = Light Emitting Diode\index{Light Emitting Diode!\Siehe {LED}},
}

%%%%%%%%%%%%%%%%%%%%%%%%%%%%%%%%%%%%%%%%%%%%%%%%%%%%%
% M
%%%%%%%%%%%%%%%%%%%%%%%%%%%%%%%%%%%%%%%%%%%%%%%%%%%%%

\DeclareAcronym{mimd}{
    short = MIMD \index{MIND},
    long  = Multiple-Instruction Multiple-Data\index{Multiple-Instruction Multiple-Data!\Siehe MIMD} ,
}

\DeclareAcronym{nn}{
    short = NN, 
    long  = Neuronales Netz,
}

\DeclareAcronym{nfc}{
	short = NFC\index{NFC},
	long  = Near Field Communication\index{Near Field Communication!\Siehe {NFC}} ,
}

%%%%%%%%%%%%%%%%%%%%%%%%%%%%%%%%%%%%%%%%%%%%%%%%%%%%%
% N
%%%%%%%%%%%%%%%%%%%%%%%%%%%%%%%%%%%%%%%%%%%%%%%%%%%%%

%%%%%%%%%%%%%%%%%%%%%%%%%%%%%%%%%%%%%%%%%%%%%%%%%%%%%
% O
%%%%%%%%%%%%%%%%%%%%%%%%%%%%%%%%%%%%%%%%%%%%%%%%%%%%%

\DeclareAcronym{opencl}{
    short = OpenCL\index{OpenCL}, 
    long  = Open Computing Language\index{Open Computing Language!\Siehe OpenCL},
}

\DeclareAcronym{oled}{
	short = OLED\index{OLED}, 
	long  = Organic Light Emitting Diode\index{Organic Light Emitting Diode!\Siehe OLED},
}

%%%%%%%%%%%%%%%%%%%%%%%%%%%%%%%%%%%%%%%%%%%%%%%%%%%%%
% P
%%%%%%%%%%%%%%%%%%%%%%%%%%%%%%%%%%%%%%%%%%%%%%%%%%%%%

\DeclareAcronym{pan}{
	short = PAN\index{PAN} ,
	long  = Path Aggregation Network\index{Path Aggregation Network!\Siehe PAN} ,
}

\DeclareAcronym{pdm}{
	short = PDM\index{PDM} ,
	long  = Pulsdichtenmodulation\index{Pulsdichtenmodulation!\Siehe PDM} ,
}

\DeclareAcronym{ppa}{
    short = PPA\index{PPa}, 
    long  = Personal Package Archive\index{Personal Package Archive!\Siehe PPA},
}

\DeclareAcronym{pip}{
	short = pip\index{pip} ,
	long  = pip installs packages\index{pip installs packages!\Siehe pip} ,
}

\DeclareAcronym{pypi}{
	short = PyPi\index{PyPi} ,
	long  = Python Package Index\index{Python Package Index!\Siehe PyPi} ,
}

%%%%%%%%%%%%%%%%%%%%%%%%%%%%%%%%%%%%%%%%%%%%%%%%%%%%%
% Q
%%%%%%%%%%%%%%%%%%%%%%%%%%%%%%%%%%%%%%%%%%%%%%%%%%%%%

%%%%%%%%%%%%%%%%%%%%%%%%%%%%%%%%%%%%%%%%%%%%%%%%%%%%%
% R
%%%%%%%%%%%%%%%%%%%%%%%%%%%%%%%%%%%%%%%%%%%%%%%%%%%%%

\DeclareAcronym{ram}{
	short = RAM\index{RAM} ,
	long  = Random Access Memory\index{Random Access Memory! \Siehe RAM},
}

\DeclareAcronym{relu}{
    short = ReLu\index{ReLu}, 
    long  = Rectified Linear Unit\index{Rectified Linear Unit!\Siehe ReLu},
}

\DeclareAcronym{resnets}{
    short = ResNet\index{ResNet},
    long =  Residual Neural Network\index{Residual Neural Network!\Siehe ResNet},
}    

\DeclareAcronym{rle}{
    short = RLE\index{RLE},
    long  = Run-Length Encoding\index{Run-Length Encoding},
}

\DeclareAcronym{rgb}{
  short = RGB,
  long  = Rot-Grün-Blau}

\DeclareAcronym{roi}{
	short = ROI\index{Region of Interest},
	long  = Region of Interest\index{Region of Interest}
}

\DeclareAcronym{rpc}{
	short = RPC\index{RPC}, 
	long  = Remote call procedure\index{Remote call procedure!\Siehe RPC},
}

\DeclareAcronym{RTOS}{
	short = RTOS\index{RTOS}, 
	long  = Real Time Operating System\index{Real Time Operating System!\Siehe RTOS},
}

%%%%%%%%%%%%%%%%%%%%%%%%%%%%%%%%%%%%%%%%%%%%%%%%%%%%%
% S
%%%%%%%%%%%%%%%%%%%%%%%%%%%%%%%%%%%%%%%%%%%%%%%%%%%%%

\DeclareAcronym{sd}{
  short = SD\index{SD},
  long  = Secure Digital\index{Secure Digital!\Siehe SD},
}

\DeclareAcronym{sda}{
    short = SDA\index{SDA},
    long  = Serial Data\index{Serial Data!\Siehe SDA},
}    

\DeclareAcronym{sd-1}{
    short = SD-1\index{Datensatz!NIST~Special~Database~1},
    long  = NIST Special Database~1\index{NIST Special Database 1!\Siehe Datensatz},
}    

\DeclareAcronym{sd-3}{
    short = SD-3\index{Datensatz!NIST Special Database 3},
    long  = NIST Special Database 3\index{NIST Special Database 3!\Siehe Datensatz},
}    

\DeclareAcronym{scl}{
    short = SCL\index{SCL},
    long  = Serial Clock\index{Serial Clock!\Siehe SCL},
}    

\DeclareAcronym{ssh}{
    short = SSH\index{SSH},
    long  = Secure Shell\index{Secure Shell!\Siehe SSH},
}

\DeclareAcronym{spi}{
    short = SPI\index{SPI},
    long  = Serial Peripheral Interface\index{Serial Peripheral Interface!\Siehe SPI},
}

\DeclareAcronym{sbc}{
    short = SBC\index{SBC} ,
    long  = Single-Board-Computer\index{Single-Board-Computer!\Siehe SBC} ,
}

\DeclareAcronym{simd}{
	short = SIMD\index{SIMD} ,
	long  = Single-Instruction Multiple-Data\index{Single-Instruction Multiple-Data!\Siehe SIMD} ,
}

\DeclareAcronym{sm}{
	short = SM\index{SM} ,
	long  = Streaming Multiprocessor\index{Streaming Multiprocessor!\Siehe SM} ,
}

\DeclareAcronym{smd}{
	short = SMD\index{SMD} ,
	long  = Surface Mount Device\index{Surface Mount Device!\Siehe SMD} ,
}

\DeclareAcronym{sp}{
	short = SP\index{SP} ,
	long  = Streaming Processor\index{Streaming Processor!\Siehe SP} ,
}

\DeclareAcronym{spp}{
	short = SP\index{SP} ,
	long  = Streaming Processor\index{Streaming Processor!\Siehe SP} ,
}

\DeclareAcronym{sps}{
    short = SPS\index{SPS} ,
    long  = Speicherprogrammierbare Steuerung\index{Speicherprogrammierbare Steuerung!\Siehe SPS} ,
}

\DeclareAcronym{soc}{
short = SoC\index{SoC} ,
long  = System on Chip\index{System on Chip!\Siehe SoC} ,
}

%%%%%%%%%%%%%%%%%%%%%%%%%%%%%%%%%%%%%%%%%%%%%%%%%%%%%
% T
%%%%%%%%%%%%%%%%%%%%%%%%%%%%%%%%%%%%%%%%%%%%%%%%%%%%%

\DeclareAcronym{tpu}{
	short = TPU\index{TPU}, 
	long  = Tensor Processing Unit\index{Tensor Processing Unit!\Siehe TPU},
}

%%%%%%%%%%%%%%%%%%%%%%%%%%%%%%%%%%%%%%%%%%%%%%%%%%%%%
% U
%%%%%%%%%%%%%%%%%%%%%%%%%%%%%%%%%%%%%%%%%%%%%%%%%%%%%

\DeclareAcronym{uart}{
    short = UART\index{UART}, 
    long  = Universal Asynchronous Receiver Transmitter\index{Universal Asynchronous Receiver Transmitter!\Siehe UART},
}

\DeclareAcronym{ui}{
	short = UI\index{UI},
	long = user interface\index{user interface!\Siehe UI},
}

\DeclareAcronym{uma}{
  short = UMA\index{UMA}, 
  long  = Unified Memory Architecture\index{Unified Memory Architecture!\Siehe UMA},
}

\DeclareAcronym{musb}{
	short = Micro USB\index{Micro USB},
	long = Micro Universal Serial Bus\index{Micro Universal Serial Bus!\Siehe {Micro USB}},
}

\DeclareAcronym{uv}{
	short = UV-Filter\index{Micro USB},
	long = Ultravioletter-Filter\index{Ultravioletter-Filter!\Siehe {Micro USB}},
}

%%%%%%%%%%%%%%%%%%%%%%%%%%%%%%%%%%%%%%%%%%%%%%%%%%%%%
% V
%%%%%%%%%%%%%%%%%%%%%%%%%%%%%%%%%%%%%%%%%%%%%%%%%%%%%

\DeclareAcronym{venv}{
    short = VENV\index{VENV} ,
    long  = Virtual Environment\index{Virtual Environment!\Siehe VENV} ,
}

\DeclareAcronym{vpu}{
  short = VPU\index{VPU},
  long  = Video Processing Unit\index{Video Processing Unit!\Siehe VPU},
}

\DeclareAcronym{vm}{
	short = VM\index{VM},
	long  = Virtual Machine\index{Virtual Machine!\Siehe VM},
}

\DeclareAcronym{vnc}{
	short = VNC\index{VNC} ,
	long  = Virtual Network Computing\index{Virtual Network Computing!\Siehe VNC} ,
}

%%%%%%%%%%%%%%%%%%%%%%%%%%%%%%%%%%%%%%%%%%%%%%%%%%%%%
% W
%%%%%%%%%%%%%%%%%%%%%%%%%%%%%%%%%%%%%%%%%%%%%%%%%%%%%

%%%%%%%%%%%%%%%%%%%%%%%%%%%%%%%%%%%%%%%%%%%%%%%%%%%%%
% X
%%%%%%%%%%%%%%%%%%%%%%%%%%%%%%%%%%%%%%%%%%%%%%%%%%%%%

%%%%%%%%%%%%%%%%%%%%%%%%%%%%%%%%%%%%%%%%%%%%%%%%%%%%%
% Y
%%%%%%%%%%%%%%%%%%%%%%%%%%%%%%%%%%%%%%%%%%%%%%%%%%%%%

\DeclareAcronym{yolo}{
	short = YOLO\index{YOLO},
	long  = You Only Look Once\index{You Only Look Once!\Siehe YOLO},
}

%%%%%%%%%%%%%%%%%%%%%%%%%%%%%%%%%%%%%%%%%%%%%%%%%%%%%
% Z
%%%%%%%%%%%%%%%%%%%%%%%%%%%%%%%%%%%%%%%%%%%%%%%%%%%%%

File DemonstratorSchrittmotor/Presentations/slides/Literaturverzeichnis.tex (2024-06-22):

%%%%%%%%%%%%%%%%%%%%
%
% $Beschreibung: Das Literaturverzeichnis nocheinmal in detaillierter Form $
% $Autor: ter Veen $
% $Datum: 15.06.2024 $
% $Pfad: DemonstratorSchrittmotor/Presentations/slides/Literaturverzeichnis.tex $
% $Version: 1 $
%
%%%%%%%%%%%%%%%%%%%

\Mysection{Detailliertes Literaturverzeichnis}

\STANDARD{Adafruit Industries (2024):}
{
	\begin{minipage}{0.38\textwidth}
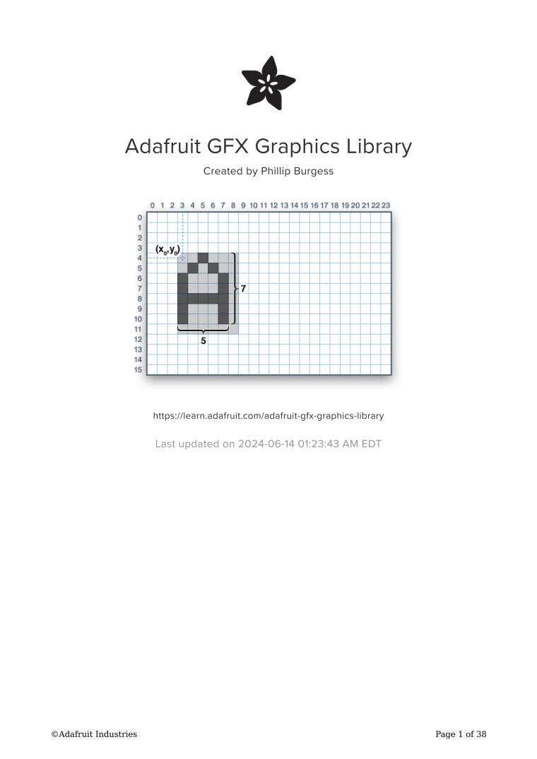
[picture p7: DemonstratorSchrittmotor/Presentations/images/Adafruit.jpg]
		
	\end{minipage}
	\hfill
	\begin{minipage}{0.6\textwidth}
		Internetdokument. Adafruit GFX Library. Zuletzt aktualisiert am 2024, zuletzt geprüft am 21.06.2024.
		\\ \textbf{Kurzfassung:}
		Die Adafruit GFX-Bibliothek für Arduino bietet eine einheitliche Syntax und einen Satz von Grafikfunktionen für all unsere LCD- und OLED-Displays sowie LED-Matrizen. Dadurch können Arduino-Skizzen mit minimalem Aufwand zwischen verschiedenen Displaytypen angepasst werden.
	\end{minipage}
	\textbf{Schlagwörter:}
	Display; OLED; Programming
	\\ \textbf{Bewertung:}
	Die Dokumentation war hilfreich für die Anbindung des OLED-Displays´s.
}

\STANDARD{Adafruit Industries (2024)b:}
{
	\begin{minipage}{0.38\textwidth}
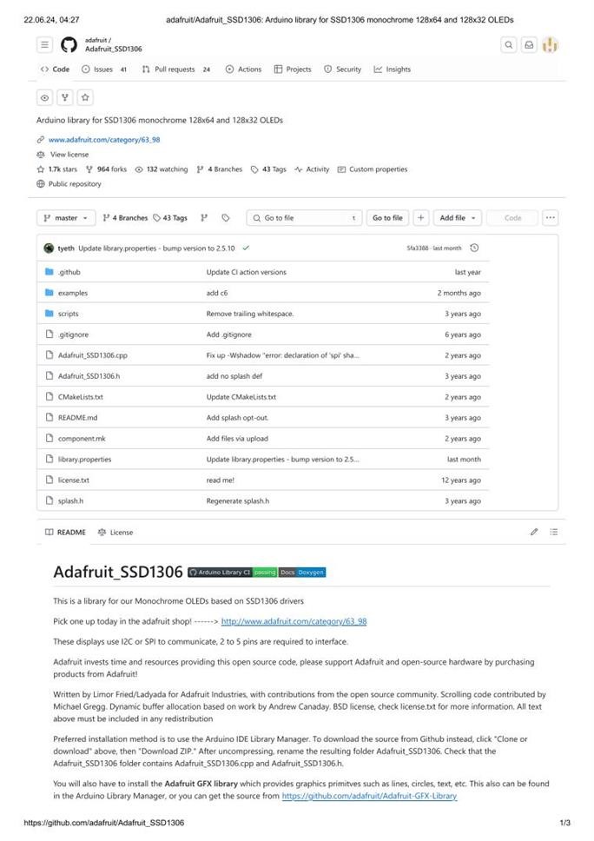
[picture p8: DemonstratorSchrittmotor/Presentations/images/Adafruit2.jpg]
		
	\end{minipage}
	\hfill
	\begin{minipage}{0.6\textwidth}
		Internetdokument. Adafruit SSD1306 Library. Zuletzt aktualisiert am 2024, zuletzt geprüft am 21.06.2024.
		\\ \textbf{Kurzfassung:}
	Dokumentation für die Adafruit SSD1306 Bibliothek. Dies ist eine Bibliothek speziell für die Ansteuerung von OLEDs, die auf SSD1306 Treibern basieren.
	\end{minipage}
	\textbf{Schlagwörter:}
	Display; OLED; Programming
	\\ \textbf{Bewertung:}
	Die Dokumentation war hilfreich für die Anbindung des OLED-Displays´s.
}

\STANDARD{Adcanced Monolithic System (2024):}
{
\begin{minipage}{0.38\textwidth}
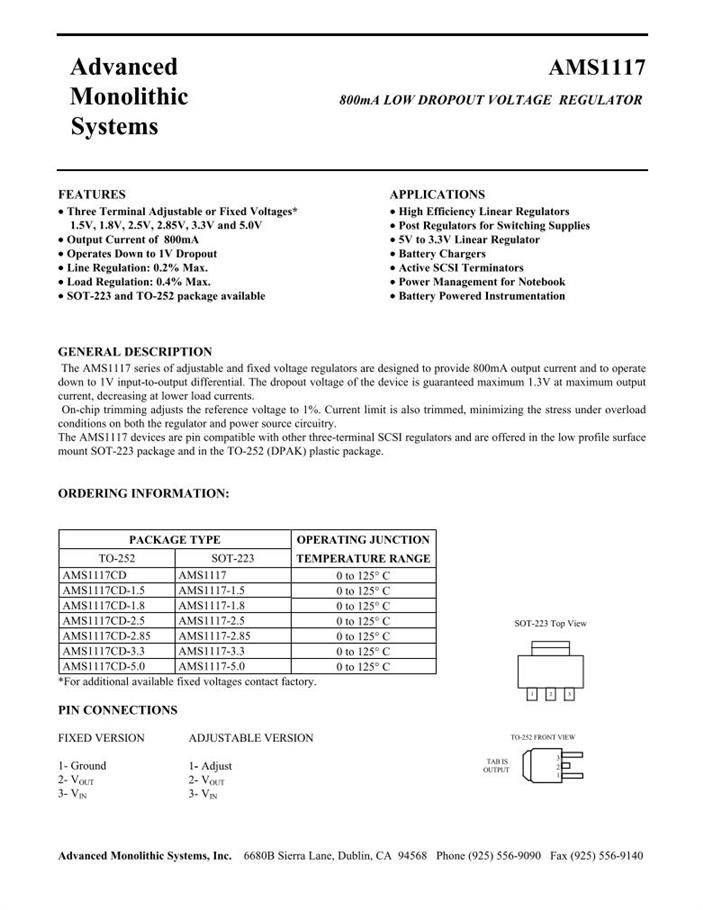
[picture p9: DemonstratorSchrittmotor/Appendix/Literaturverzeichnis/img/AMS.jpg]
	
\end{minipage}
\hfill
\begin{minipage}{0.6\textwidth}
Internetdokumentation. AMS1117 ADMOS | Alldatasheet. 800mA LOW DROPOUT VOLTAGE REGULATOR.
Online verfügbar unter http://www.advanced-monolithic.com/pdf/ds1117.pdf, zuletzt aktualisiert am 2024, zuletzt geprüft am 11.04.2024.
\\ \textbf{Kurzfassung:}
Das Datenblatt für den Spannungswandler AMS1117. Alle notwendigen Angaben, wie minimal/maximal Eingangs- zu Ausgangsspannung und Ausgangsstrom sind angegeben. Darüber hinaus sind noch viele weitere Informationen angegeben, wie z.B. Pin-Belegung, Temperaturverhalten, usw.
\end{minipage}
\textbf{Schlagwörter:}
3.3 V; 5 V; ALLDATASHEET; ARCHIVE; CATALOG; CHIP; DATABOOK; Datasheet; ELECTRONIC COMPONENT; IC; ISO COMPONENT; PDF; PDF DATASHEET; SEMICONDUCTOR; TRANSISTOR
\\ \textbf{Bewertung:}
Das Datenblatt bietet alle notwendigen Angaben, welche benötigt werden. Optimal wäre noch ein zusätzlich Datenblatt in deutscher Übersetzung gewesen.
}

\STANDARD{Allegro (2022):}
{
\begin{minipage}{0.38\textwidth}
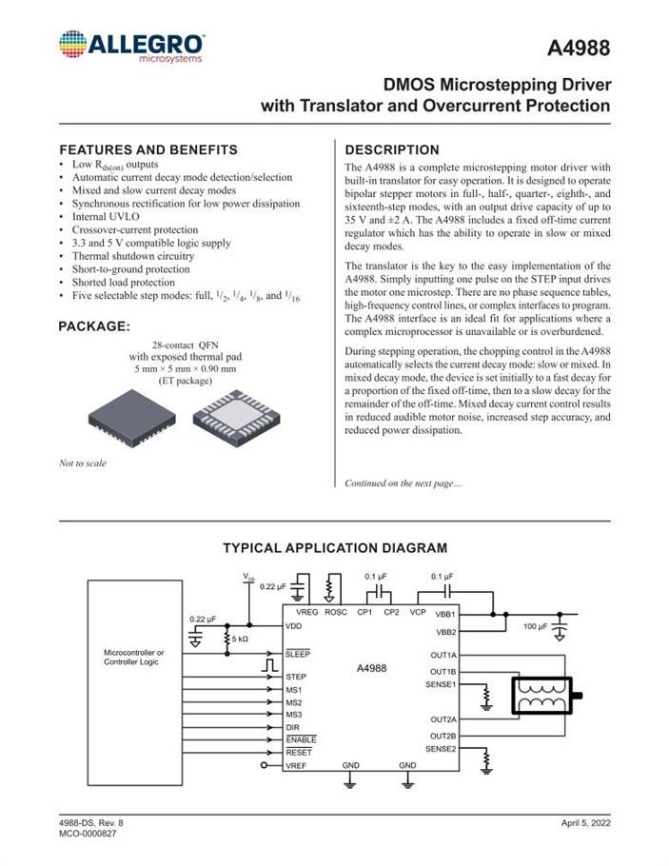
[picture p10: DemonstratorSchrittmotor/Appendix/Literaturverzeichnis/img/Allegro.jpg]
	
\end{minipage}
\hfill
\begin{minipage}{0.6\textwidth}
Internetdokumentation. A4988-Datasheet.
Online verfügbar unter https://www.allegromicro.com, zuletzt aktualisiert am 2022, zuletzt geprüft am 08.04.2024.
\\ \textbf{Kurzfassung:}
Datenblatt für die Schrittmotorsteuerung A4988. Es sind viele wichtige Informationen zur Inbetriebnahme des Schrittmotors angegeben: Die Logic Strom Versorgung ist mit 3.3 und 5 V möglich, 5 Schritt-Modis (step modes), Last-Versorgungsspannung mit bis zu 35 V und die Pin-Belegung.
\end{minipage}
\textbf{Schlagwörter:}
5 step modes; A4988; Motorsteuerung; Pin-Belegung; Schrittmotorsteuerung; Treiber
\\ \textbf{Bewertung:}
Das Datenblatt beinhaltet alle notwendigen Informationen für eine korrekte Inbetriebnahme.
}

\STANDARD{Arduino (2024):}
{
\begin{minipage}{0.38\textwidth}
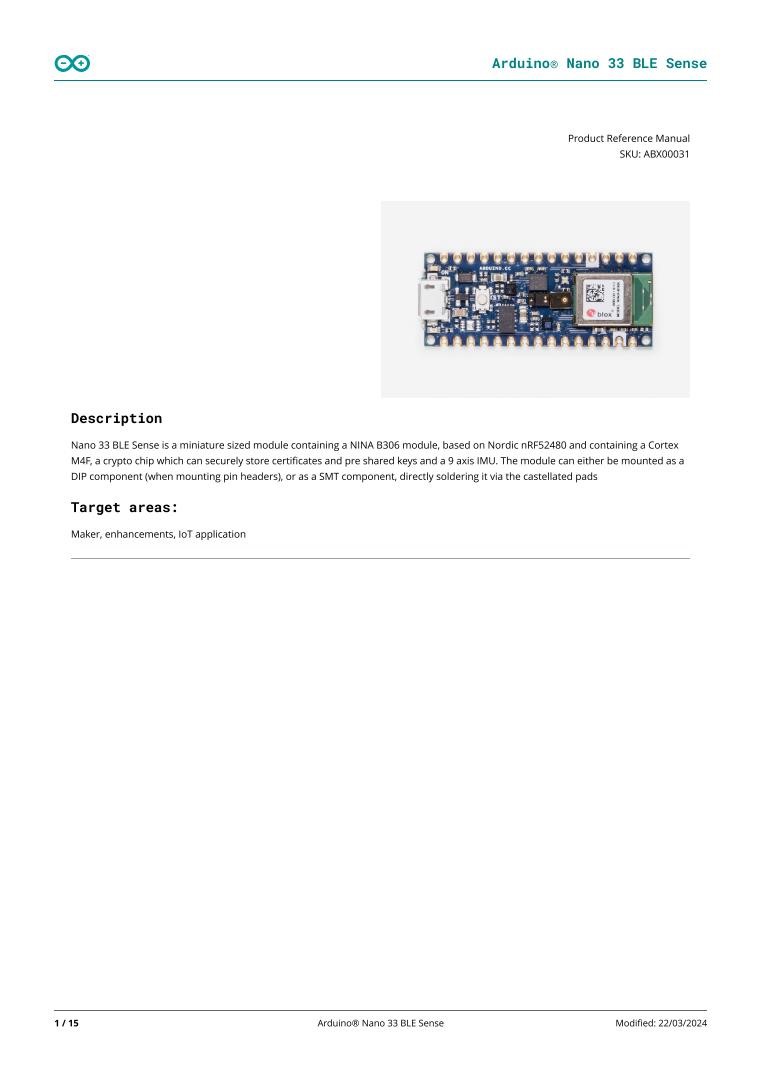
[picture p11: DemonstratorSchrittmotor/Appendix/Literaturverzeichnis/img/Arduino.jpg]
	
\end{minipage}
\hfill
\begin{minipage}{0.6\textwidth}
Internetdokumentation. ABX00031-Datasheet
zuletzt aktualisiert am 2024.
\\ \textbf{Kurzfassung:}
Eine detailliertes aber gut verständliches Handbuch zum Arduino Nano 33 BLE Sense. Mithilfe des Handbuches kann der Mikrocontroller fachgerecht in ein System integriert werden. Es wird außerdem ein kurzer Überblick aller im Arduino integrierten Sensoren gegeben.	
\end{minipage}
\textbf{Schlagwörter:}
Arduino; Arduino Nano 33 BLE Sense; Mikrocontroller; nicht 5 V verträglich; NRF52 Series; Pin-Belegung; Sensorik
\\ \textbf{Bewertung:}
Das Handbuch ist gut geeignet, um einen Überblick der Funktionen des Arduinos zu bekommen und es zu verdrahten. Jedoch sind die Funktionen der Sensoren und Peripherie-Geräte relativ kurz gehalten.
}

\STANDARD{Arduino IDE Dokumentation (2024) mehrere Einträge:}
{
	
\begin{itemize}
	\item \textbf{Downloads. Arduino IDE 2.3.2:}
	Hg. v. Arduino. https://www.arduino.cc/en/software. Online verfügbar unter https://www.arduino.cc/en/software, zuletzt geprüft am 12.04.2024.
	\item \textbf{Installing a Board Package in the IDE 2:}
	Hg. v. Arduino. Online verfügbar unter https://docs.arduino.cc/software/ide-v2/tutorials/ide-v2-board-manager., zuletzt aktualisiert am 16.04.2024, zuletzt geprüft am 13.06.2024.
	\item \textbf{Installing Libraries:}
	Hg. v. Arduino. Online verfügbar unter https://docs.arduino.cc/software/ide-v2/tutorials/ide-v2-installing-a-library/, zuletzt aktualisiert am 12.02.2024, zuletzt geprüft am 12.04.2024.
	\item \textbf{loop:} Hg. v. Arduino. Online verfügbar unter https://docs.arduino.cc/software/ide-v2/tutorials/ide-v2-installing-a-library/, zuletzt aktualisiert am 12.02.2024, zuletzt geprüft am 12.04.2024.
	\item \textbf{setup:} Hg. v. Arduino. Online verfügbar unter https://www.arduino.cc/reference/en/language/structure/sketch/setup/, zuletzt geprüft am 12.04.2024.
	\item \textbf{Blink:} Blink. Turn an LED on and off every second. Hg. v. Arduino. Online verfügbar unter https://docs.arduino.cc/built-in-examples/basics/Blink/, zuletzt aktualisiert am 02.09.2022.	
	\item \textbf{Debounce on a Pushbutton:} Hg. v. Arduino. Online verfügbar unter https://docs.arduino.cc/built-in-examples/digital/Debounce/, zuletzt aktualisiert am	02.09.2022.
\end{itemize}
\textbf{Kurzfassung:}
Die Arduino Software Dokumentation zur IDE ist eine Sammlung an Informationen, die Anwendern dabei hilft, sich mit der Arduino-Entwicklungsumgebung vertraut zu machen, ihre Programmierkenntnisse zu erweitern und Projekte zu realisieren. 
\\ \textbf{Schlagwörter:}
Arduino; Dokumentation; DIE; loop; setup; download; packages; libaries; Tasterfunktion; Blink
\\ \textbf{Bewertung:}
Die Dokumentation auf der Arduino ist für Anfänger leicht zugänglich und bietet auch fortgeschrittenen Benutzern wertvolle Informationen und Unterstützung. Jedoch müssen gute Englischkenntnisse vorliegen, da keine Übersetzung in deutsch vorliegt.
}

\STANDARD{Arm (2020):}
{
\begin{minipage}{0.38\textwidth}
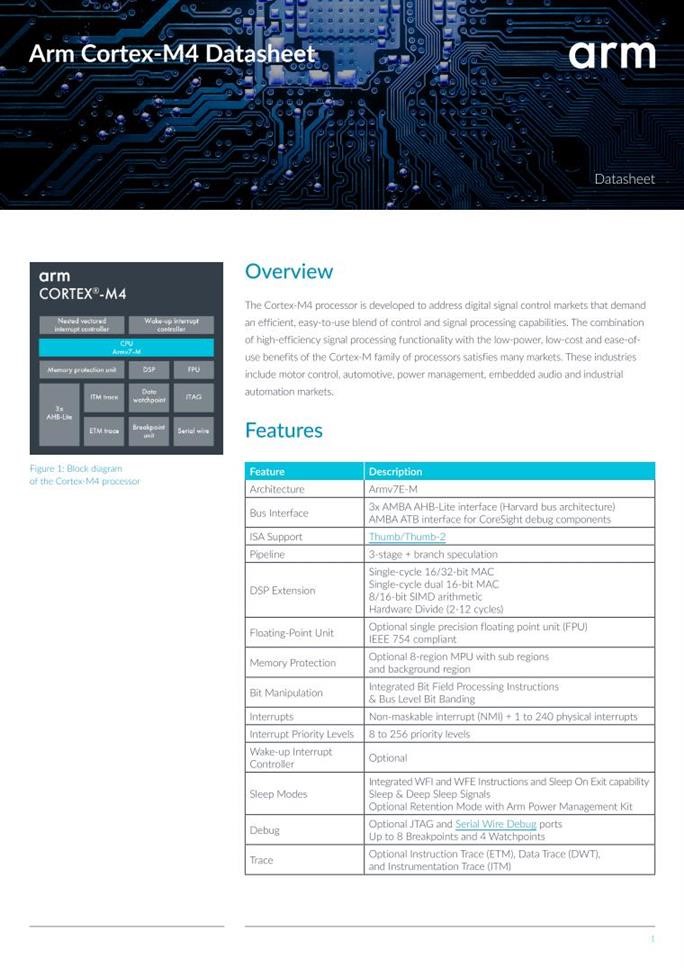
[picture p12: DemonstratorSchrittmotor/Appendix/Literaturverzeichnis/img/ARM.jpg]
	
\end{minipage}
\hfill
\begin{minipage}{0.6\textwidth}
Internetdokument. Arm-Cortex-M4-Processor-Datasheet. Zuletzt aktualisiert am 2020.
\\ \textbf{Kurzfassung:}
Datenblatt für den Arm Cortex-M4 Prozessor.	
\\ \textbf{Schlagwörter:}
ArmCortex M4; Cortex-M4; Datasheet; Datenblatt; Prozessor
\\ \textbf{Bewertung:}
Ausführliches Datenblatt mit vielen weiteführenden Informationen zum Prozessor.
\end{minipage}
}

\STANDARD{Avago Technologies (2015):}
{
\begin{minipage}{0.38\textwidth}
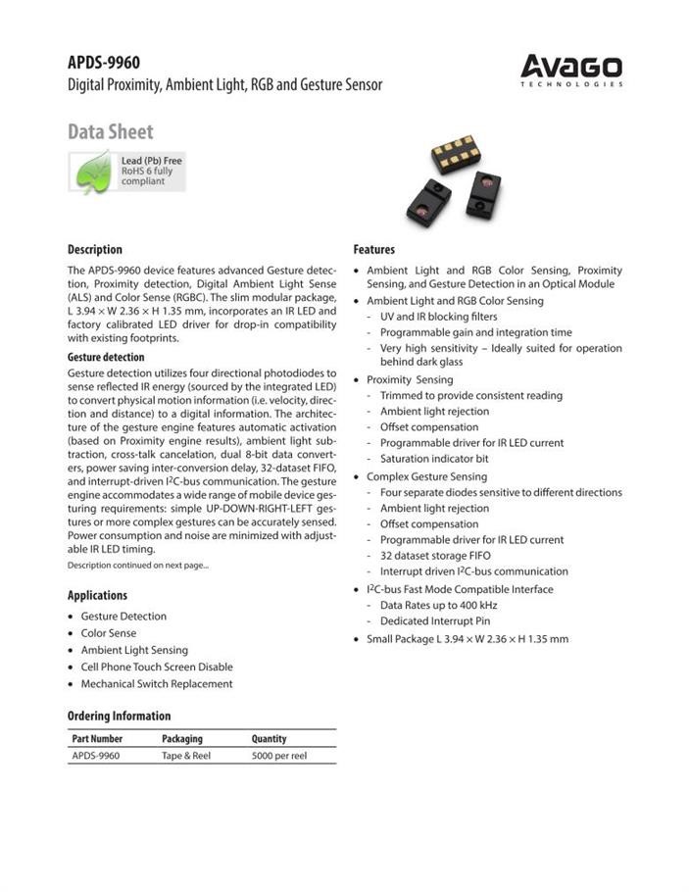
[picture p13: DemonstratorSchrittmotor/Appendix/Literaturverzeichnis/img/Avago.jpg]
	
\end{minipage}
\hfill
\begin{minipage}{0.6\textwidth}
Internetdokument. Datasheet - APDS-9960 - Digital Proximity, Ambient Light, RGB and Gesture Sensor. Zuletzt aktualisiert am 2015.
\\ \textbf{Kurzfassung:}
Datenblatt zum Näherungs-, Umgebungslicht-, Farb- und Gestensensor.
Weiterführende Informationen zum Sensor.
\\ \textbf{Schlagwörter:}
APDS-9960; Datasheet; Datenblatt; Farbsensor; Lichtsensor; Näherungssensor; Sensorik
\\ \textbf{Bewertung:}
Detailliertes Datenblatt zum APDS-9960 Sensor zur besseren Verständlichkeit.
\end{minipage}
}

\STANDARD{AZ-Delivery (2024):}
{
\begin{minipage}{0.38\textwidth}
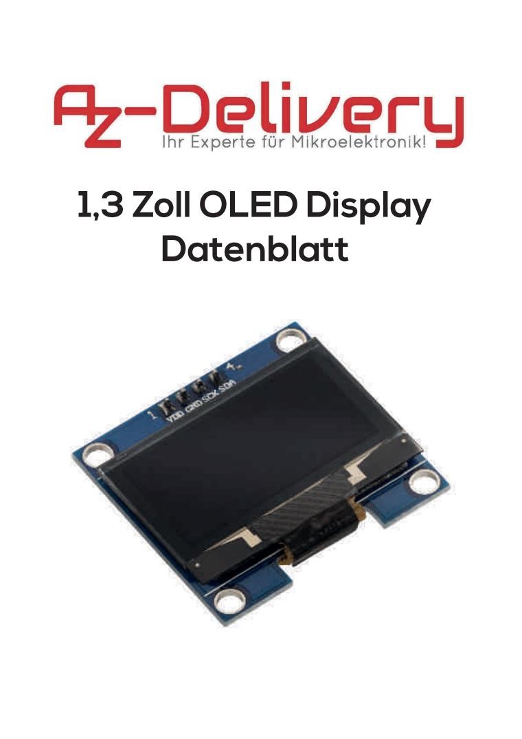
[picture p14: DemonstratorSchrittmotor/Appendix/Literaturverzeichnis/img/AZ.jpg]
	
\end{minipage}
\hfill
\begin{minipage}{0.6\textwidth}
Internetdokument. 1,3 Zoll OLED Display Datenblatt.
Hg. v. AZ-Delivery. Online verfügbar unter https://www.az-delivery.de/products/1-3zoll-i2c-oled-display, zuletzt geprüft am 26.04.2024.
\\ \textbf{Kurzfassung:}
Datenblatt zum OLED Display. Das Datenblatt enthält alle wichtigen Daten zur Integration des Displays und noch Informationen darüber hinaus.	
\\ \textbf{Schlagwörter:}
Bildschirm; Datasheet; Datenblatt; I2C; OLED
\\ \textbf{Bewertung:}
Gerade für die Systemintegration des Bildschirms, war das Datenblatt hilfreich, da alle Anschluss-Pins angegeben sind und die Bauteil Abmaße angegeben sind.
\end{minipage}
}

\STANDARD{Babiel, Gerhard (2023):}
{
Buch (Monographie). Elektrische Antriebe in der Fahrzeugtechnik. Lehr- und Arbeitsbuch.
5. Auflage. Wiesbaden, Heidelberg: Springer Vieweg.	
\begin{minipage}{0.38\textwidth}
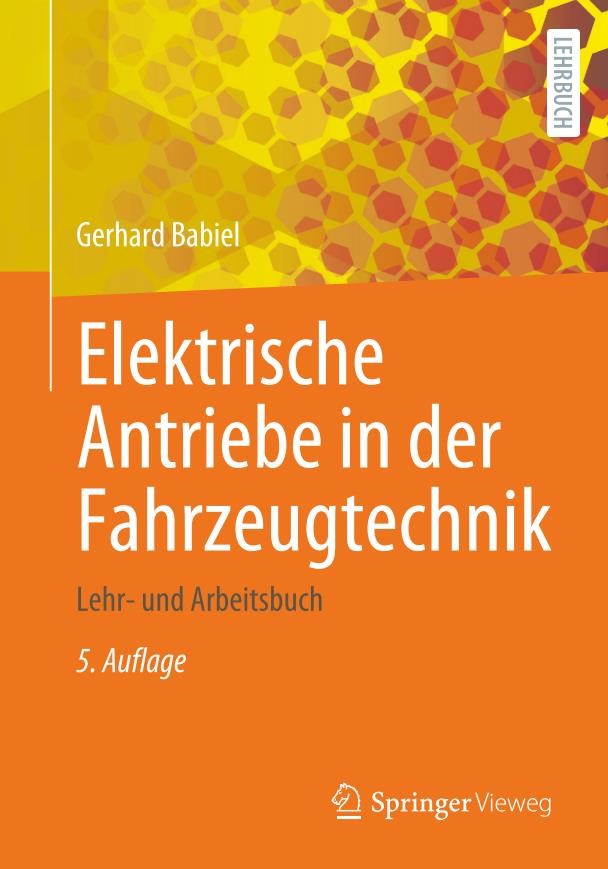
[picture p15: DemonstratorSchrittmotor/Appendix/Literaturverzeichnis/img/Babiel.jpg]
	
\end{minipage}
\hfill
\begin{minipage}{0.6\textwidth}
\textbf{Kurzfassung:}
Das Lehrbuch vermittelt die Grundlagen von der Energiegewinnung über die Energiewandlung bis zur Drehfeldmaschine und deren Anwendung in heutigen und vor allem zukünftigen Antriebssystemen. Zunächst werden aktuelle und zukünftige Energiequellen für Fahrzeugantriebe vorgestellt und miteinander verglichen. Darauf aufbauend werden elektrochemische Energiespeicher und -wandler wie die Wasserstoff-Brennstoffzelle behandelt. Es werden Gleichstrom-, Asynchron-, Synchron- und Linearmotor sowie Reluktanz-, Transversalfluss- und Digital-Motoren erklärt. Im letzten Kapitel werden Antriebssysteme am Beispiel einer E-Lok und der Magnetschwebebahn vorgestellt.
\end{minipage}
\textbf{Schlagwörter:}
Elektromotor; Mikroschrittverfahren; Positioniergenauigkeit; PWM; Schrittmotor
\\ \textbf{Bewertung:}
Das Lehrbuch ist ein umfassendes Lehrbuch für elektrische Antriebe. Für dieses Projekt wurden lediglich Auszüge aus dem Teil \glqq Schrittmotoren \grqq verwendet.
\\ \textbf{ISBN:}
978-3-658-40585-4
}

\STANDARD{Basler, Stefan (2016):}
{
Buch (Monographie). Encoder und Motor-Feedback-Systeme.
Wiesbaden: Springer Fachmedien Wiesbaden. Online verfügbar unter https://link.springer.com/book/10.1007/978-3-658-12844-9 \\
zuletzt geprüft am 11.04.2024.	\\
\begin{minipage}{0.38\textwidth}
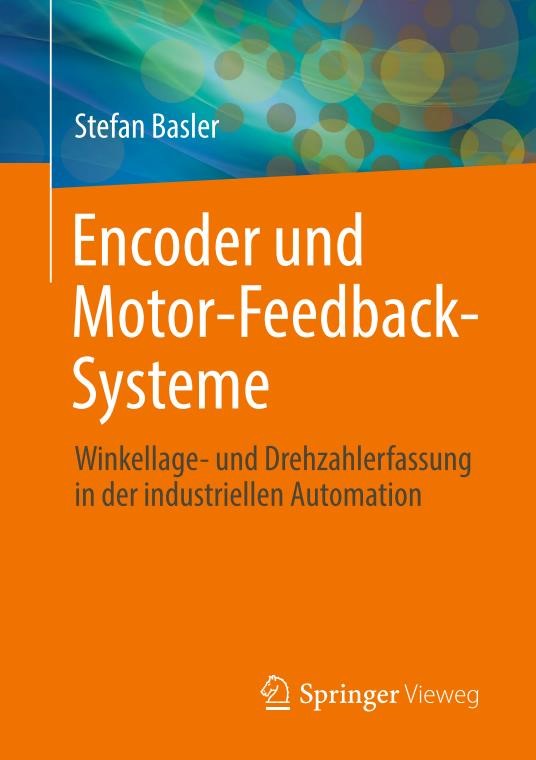
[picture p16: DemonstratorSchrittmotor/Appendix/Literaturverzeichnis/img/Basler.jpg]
	
\end{minipage}
\hfill
\begin{minipage}{0.6\textwidth}
\textbf{Kurzfassung:}
Das Buch gibt einen Einblick in die Theorie, die Sensorik, den Aufbau und die Anwendungen von Drehgebern. Encoder sind wichtige Komponenten in der Steuerungs- und Automatisierungstechnik, Motor-Feedback-Systeme in der modernen Antriebstechnik. Sie wandeln den Winkel zweier relativ zueinander drehbaren Objekte in ein elektrisches Signal um. Dies setzt man ein, um die Winkellage und die Drehzahl einer sich drehenden Achse zu erfassen. Das Wissen darüber hat eine große Bedeutung in der industriellen Automation und bei Servoantrieben.	
\end{minipage}
\textbf{Schlagwörter:}
Absolutdrehgeber; Automatisierungstechnik; Drehgeber; Encoder; Inkrementaldrehgeber; Regelungstechnik
\\ \textbf{Bewertung:}
Das Buch befasst sich sehr umfangreich mit der Thematik Drehgeber und Encoder. Mithilfe des Buches konnte die grundlegende Funktionsweise von Drehgebern errungen werden.
\\ \textbf{ISBN:}
978-3-658-12843-2
}

\STANDARD{Bernstein, Herbert (2018):}
{
Buch (Monographie). Elektrotechnik/Elektronik für Maschinenbauer. Einfach und praxisgerecht. 3., überarbeitete Auflage. \\Wiesbaden, Heidelberg: Springer Vieweg (Lehrbuch).\\
\begin{minipage}{0.38\textwidth}
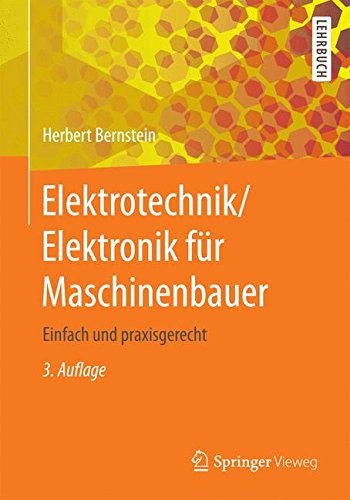
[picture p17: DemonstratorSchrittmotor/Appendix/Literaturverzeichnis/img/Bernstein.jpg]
	
\end{minipage}
\hfill
\begin{minipage}{0.6\textwidth}
\textbf{Kurzfassung:}
Dieses Lehrbuch behandelt anschaulich in Form von Beispielen oder Versuchen Gesetzmäßigkeiten beim Gleich- und Wechselstromkreis und erklärt die wichtigsten passiven Bauelemente. Es werden die wichtigsten elementaren Schaltungen zur elektrischen Messtechnik vorgestellt und die dazu benötigten analogen und digitalen Messgeräte. Grundlegende Bauelemente aus dem Bereich der Leistungshalbleiter werden mit ihren Anwendungen erklärt. Der Aufbau von Gleich-, Wechsel- und Drehstrommotoren mit Beispielen aus der Antriebstechnik wird verständlich dargestellt.
\end{minipage}
\textbf{Schlagwörter:}
Drehfeld; Elektromotor; Magnetfeld; Mikroschrittverfahren; Rotor; Schrittmotor; Stator
\\ \textbf{Bewertung:}
Herangezogen wurde dieses Buch für den Aufbau und der Funktionsweise von Schrittmotoren. Es konnte die bereits vorhanden Informationen ergänzen.
\\ \textbf{ISBN:}
978-3-658-20837-0
}

\STANDARD{Bernstein, Herbert (2020):}
{
Buch (Monographie). Mikrocontroller. Grundlagen der Hard- und Software der Mikrocontroller ATtiny2313, ATtiny26 und ATmega32.
2., aktualisierte und erweiterte Auflage.\\Wiesbaden, Heidelberg: Springer Vieweg (Lehrbuch). \\
\begin{minipage}{0.38\textwidth}
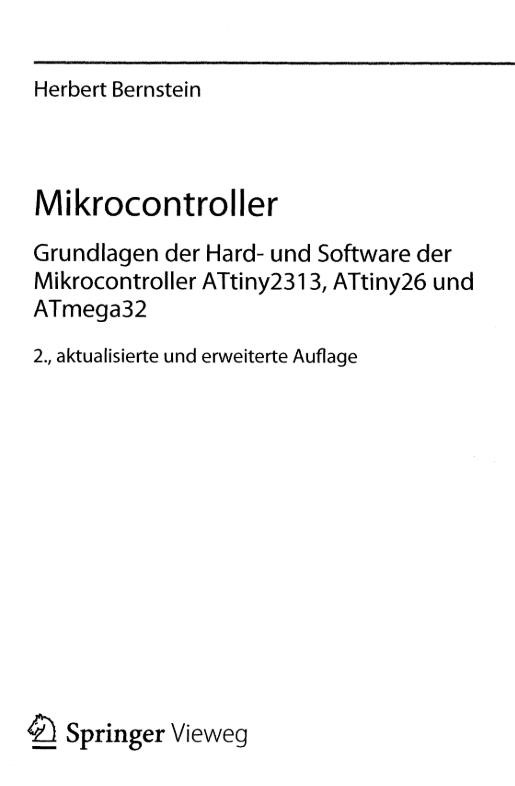
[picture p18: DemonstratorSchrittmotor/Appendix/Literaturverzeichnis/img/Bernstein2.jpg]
	
\end{minipage}
\hfill
\begin{minipage}{0.6\textwidth}
\textbf{Kurzfassung:}
Das Buch \glqq Mikrocontroller Grundlagen der Hard- und Software \grqq von Herbert Bernstein ist ein umfassendes Werk, das sich mit den Grundlagen der Mikrocontroller ATtiny2313, ATtiny26 und ATmega32 beschäftigt. Es bietet eine detaillierte Einführung in die Welt der Mikrocontroller und vermittelt sowohl theoretisches Wissen als auch praktische Anwendungen. So wird auch die Ansteuerung von Schrittmotoren mithilfe eines Mikrocontrollers behandelt.		
\end{minipage}
\textbf{Schlagwörter:}
ATmega32; ATtiny2313; ATtiny26; Bernstein; Grundlagen; I2C; IC; Mikrocontroller; Schrittmotorsteuerung
\\ \textbf{Bewertung:}
Besonders hilfreich war dieses Buch, um ein Verständnis von integrierten Schaltkreisen (I2C´s)  zu bekommen.
\\ \textbf{ISBN:}
978-3-658-30067-8
}

\STANDARD{Dieter Stotz (2019):}
{
Buch (Monographie). Computergestützte Audio- und Videotechnik. Multimediatechnik in der Anwendung. 3. Aufl. Berlin, Heidelberg: Springer Vieweg. Online verfügbar unter https://link.springer.com/book/10.1007/978-3-662-58873-4 \\zuletzt geprüft am 26.04.2024. \\
\begin{minipage}{0.38\textwidth}
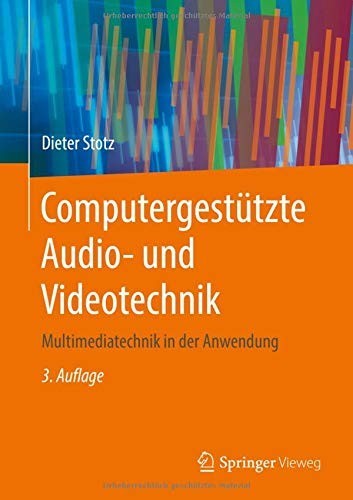
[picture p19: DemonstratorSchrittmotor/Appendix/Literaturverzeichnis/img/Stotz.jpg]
	
\end{minipage}
\hfill
\begin{minipage}{0.6\textwidth}
\textbf{Kurzfassung:}
Dieses Buch bietet eine leicht verständliche Einführung für moderne Audio- und Videotechnik im Verbund mit Computersystemen. Der Leser mit technischem Grundverständnis wird mit dem klar strukturierten Stoff einen leichten Einstieg in komplexe Zusammenhänge finden. Aus dem Inhalt: Tontechnik-Grundlagen, Abtastung und Digitalisierung, räumliches Hören, Methoden der Datenkompression, MIDI-Standard und -Signale, digitale Audiomesstechnik, Videotechnik-Grundlagen, hochauflösende Videotechnik und 3D-Technik, moderne Wiedergabesysteme (VR-Brille, OLED-Bildschirme), reales Raumsehen (Stand der Technik), Chromakeying, Schnittsysteme, Animationen, Dateienformate.	
\end{minipage}
\textbf{Schlagwörter:}
Dioden; Display; OLED
\\ \textbf{Bewertung:}
Das Buch wurde für herangezogen, um die grundlegende Funktionsweise und Vorzüge der OLED-Technik zu verstehen.
\\ \textbf{ISBN:}
978-3-662-58872-7
}

\STANDARD{Faulhaber Drive Systems (2020):}
{
\begin{minipage}{0.38\textwidth}
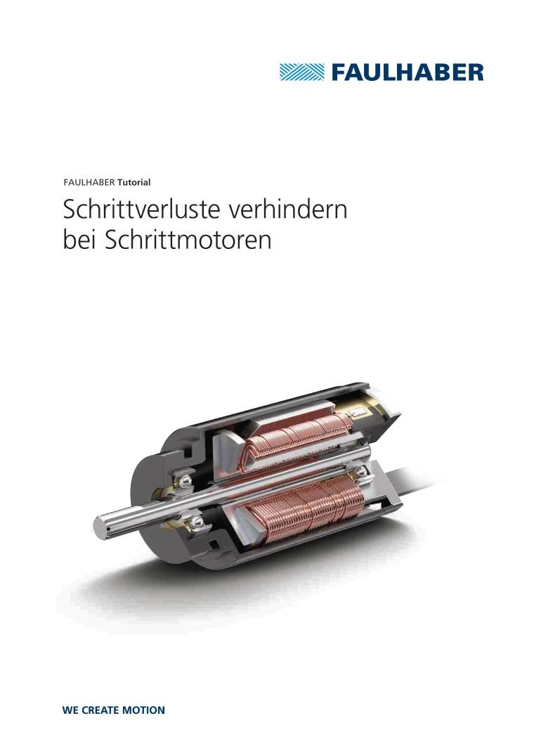
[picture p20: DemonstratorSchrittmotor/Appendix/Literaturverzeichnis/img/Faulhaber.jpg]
	
\end{minipage}
\hfill
\begin{minipage}{0.6\textwidth}
Internetdokument. Faulhaber Drive Systems (2020):
FAULHABER Tutorial. Schrittverluste verhindern bei Schrittmotoren.
Hg. v. DR. FRITZ FAULHABER GMBH \& CO. KG. Schönaich · Deutschland. Online verfügbar unter https://www.faulhaber.com/de/know-how/tutorials/schrittmotoren-tutorial-schrittverluste-verhindern-bei-schrittmotoren/, zuletzt geprüft am 14.05.2024.
\\ \textbf{Kurzfassung:}
Dieses Tutorial von Faulhaber gibt viele methodische Hinweise und Möglichkeiten, um Schrittverluste bei Schrittmotoren zu verhindern. Das Tutorial geht dabei strukturiert vor und führt durch die vier Punkte: Auswahl des Schrittmotors, Betriebsart, externe Kommutierungsfehler und externe Ereignisse.
\end{minipage}
\textbf{Schlagwörter:}
Faulhaber; Fehlerbehebung; Fehlerbilder; Lösung; Schrittmotor; Ursache
\\ \textbf{Bewertung:}
Das Tutorial war hilfreich bei der Auswahl und Inbetriebnahme des  Schrittmotors.
}

\STANDARD{Gehrke, Winfried; Winzker, Marco (2022):}
{
\begin{minipage}{0.38\textwidth}
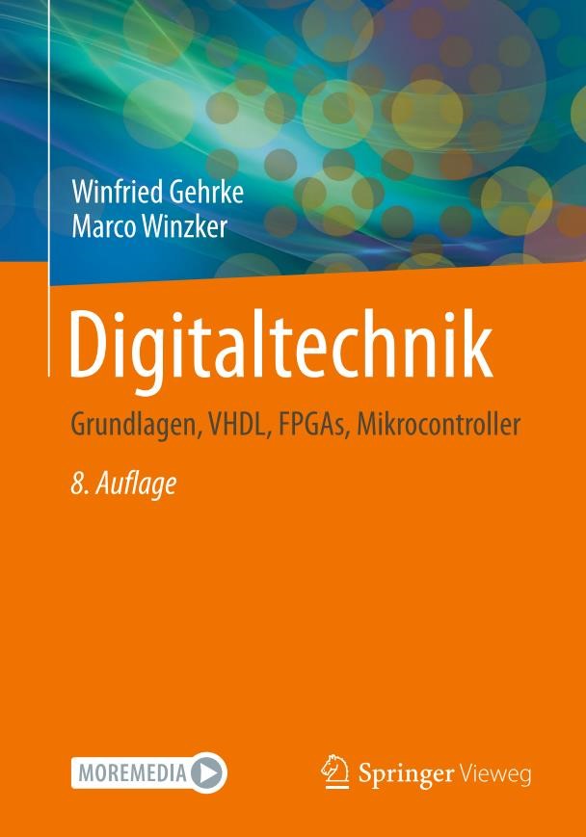
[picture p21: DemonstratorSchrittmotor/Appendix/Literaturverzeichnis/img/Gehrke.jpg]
	
\end{minipage}
\hfill
\begin{minipage}{0.6\textwidth}
Buch (Monographie). Digitaltechnik. Grundlagen, VHDL, FPGAs, Mikrocontroller.
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

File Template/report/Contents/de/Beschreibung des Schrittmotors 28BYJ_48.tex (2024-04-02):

% !TeX spellcheck = de_DE/GB

\chapter{Beschreibung des Schrittmotors 28BYJ-48}

Bist der Beste <3

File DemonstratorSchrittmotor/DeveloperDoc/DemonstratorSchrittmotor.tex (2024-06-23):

%%%%%%
% $Beschreibung: Hauptdokument für das Projekt: "Demonstrator für einen Schrittmotor", in welchem alle Seiten zusammengeführt werden $
% $Autor: ter Veen $
% $Datum: 15.04.2024 $
% $Version: 5 $
% $Pfad: SchrittmotorArduino/DevoloperDoc/DemonstratorSchrittmotor.tex $
% $Hinweis für das Literaturverzeichnis! Es muss unter Tools/Befehle/Bibtex ausgeählt werden 
%
% !TeX TXS-program:bibliography = txs:///bibtex
%%%%%%

\documentclass[12pt,a4paper]{scrbook}

% Auswahl der Sprache/Language selection
% Die nicht gewünschte Sprache muss auskommentiert werden:/The language that is not desired must be commented out:
\def\isGerman{1}
%\def\isEnglish{1}

\include{General/Packages}
\include{General/commands}
\include{General/tikzdefs}
\usepackage{circuitikz}
\usepackage{pdfpages}

\input{General/acronyms}
\input{General/Hyphenations}%
\addbibresource{../Documents/Myliterature.bib}

\begin{document}

\InputLanguage{Contents/}{Titlepage} 
\newpage

\pagenumbering{roman}

\tableofcontents
\cleardoublepage

\listoffigures
\cleardoublepage

\listoftables
\cleardoublepage

%\addcontentsline{toc}{chapter}{\TRANS{Liste der Programme}{List of Listings}}
%\lstlistoflistings
\listofcodes
\cleardoublepage

% Liste alle Listings aus Dateien
%\addcontentsline{toc}{chapter}{\TRANS{Liste der Programme}{List of Listings}}
%\lstlistoflistings
%\cleardoublepage

\addcontentsline{toc}{chapter}{Acronyms}
\printacronyms
\cleardoublepage
 
\InputLanguage{Contents/}{Symbols}

\printnomenclature
\cleardoublepage

\pagenumbering{arabic}

\cleardoublepage
\InputLanguage{Contents/}{Projektbeschreibung}

\cleardoublepage
\InputLanguage{Contents/}{HardwarebeschreibungArduino}

\cleardoublepage
\InputLanguage{Contents/}{Schrittmotorbeschreibung}

\cleardoublepage
\InputLanguage{Contents/}{WeitereHardware}

\cleardoublepage
\InputLanguage{Contents/}{SoftwarebeschreibungIDE}

\cleardoublepage
\InputLanguage{Contents/}{SchrittmotorProgrammbeschreibung}

\cleardoublepage
\InputLanguage{Contents/}{Konstruktion}

\cleardoublepage
\InputLanguage{Contents/}{Testdurch}

\cleardoublepage
\InputLanguage{Contents/}{OffenePunkte}

\cleardoublepage
\addcontentsline{toc}{chapter}{\TRANS{Literaturverzeichnis}{Bibliography}}
\printbibliography

\cleardoublepage

\addcontentsline{toc}{chapter}{Anhang}
\chapter*{Anhang}

\input{../Appendix/Schaltplan.tex}

\input{../Appendix/Materialliste.tex}

%\renewcommand{\indexname}{\TRANS{Stichwortverzeichnis}{Index}}
%\addcontentsline{toc}{chapter}{\TRANS{Stichwortverzeichnis}{Index}}
\printindex
\end{document}

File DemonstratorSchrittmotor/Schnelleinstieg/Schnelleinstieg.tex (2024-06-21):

%%%%%%%%%%%%
% $Beschreibung: Kurzfassung des Handbuchs für einen schnellen Einstieg 
% $Autor: Theilmann $
% $Datum: 16.06.2024 $
% $Pfad: DemonstratorSchrittmotor\Schnelleinstieg\Schnelleinstieg.tex $
% $Version: 2 $
%
%%%%%%%%%%%%
\documentclass[12pt,a4paper]{scrbook}
\include{Packages}

\begin{document}

	\chapter{Schnelleinstieg für Demonstrator für den Schrittmotor}
	
	\section{Lieferumfang}
	
	\begin{itemize}
		\item Demonstrator Schrittmotor
		\item Netzkabel
	\end{itemize}
	
	\section{Gerät aufstellen:}
	\begin{itemize}
		\item Stellen Sie den Demonstrator auf eine ebene, feste Oberfläche.
		\item Vermeiden Sie direkte Sonneneinstrahlung sowie Wärme- oder Feuchtigkeitsquellen.
		\item Keine Gegenstände auf den Demonstrator stellen.
		\item Halten Sie den Arbeitsbereich des Demonstrators frei von Gegenständen.
	\end{itemize}
	
	\section{Inbetriebnahme}
	
	\begin{enumerate}
		\item \textbf{Riemen einstellen:}
		\begin{itemize}
			\item Spannung überprüfen indem Sie den Schlitten manuell bewegen.
			\item Es Sollten keine Schwierigkeiten oder ungewöhnliche Geräusche auftreten.
			\item Bei Problemen Schrauben der Halterung für die Welle lösen, Riemen spannen und Schrauben wieder festziehen.
		\end{itemize}
		\item \textbf{Stromversorgung:}
		\begin{itemize}
			\item Netzkabel anschließen: Kupplung in Netzbuchse, Stecker in Steckdose.
		\end{itemize}
		\item \textbf{Einschalten:}
		\begin{itemize}
			\item Gerät über Power-Schalter einschalten.
			\item Display zeigt Bitte warten und wechselt zu Bewegungsstufe 1.
			\item Status-LED leuchtet rot, wenn das System bereit ist.
		\end{itemize}
		\item \textbf{Bewegungsstufe auswählen:}
		\begin{itemize}
			\item Drehschalter drehen, um Bewegungsstufe auszuwählen.
		\end{itemize}
		\item \textbf{Starten:}
		\begin{itemize}
			\item Start-/Stopp-Taster betätigen, um den Ablauf zu starten.
		\end{itemize}
		\item \textbf{Stoppen:}
		\begin{itemize}
			\item Ablauf stoppt automatisch.
		\end{itemize}
	\end{enumerate}
	
		\section{Bewegungsablauf}
	
\fontsize{8}{10}\selectfont
\begin{tabularx}{\textwidth}{|p{3cm}|X|X|X|p{1cm}|X|}
	\hline 
	\textbf{Drehschalterstellung}  & \textbf{Bewegungsstufe} & \textbf{ \O Geschwindigkeit [mm/s]}    \\ \hline
	1 & Pendelt Von 5\ cm auf 35\ cm & 97   \\
	\hline
	2 & Pendelt Von 5\ cm auf 35\ cm & 147 \\
	\hline
	3 & Pendelt Von 5\ cm auf 35\ cm & 184 \\
	\hline
	4 & Pendelt Von 5\ cm auf 35\ cm & 223 \\
	\hline
	5 & Pendelt Von 5\ cm auf 35\ cm & 248 \\
	\hline
	6 & Pendelt Von 5\ cm auf 35\ cm & 282 \\
	\hline
	7 & Pendelt Von 5 \ cm auf 35\ cm & 307 \\
	\hline
	8 & Pendelt Von 5 \ cm auf 35\ cm & 334\\
	\hline
	9 & Pendelt Von 5 \ cm auf 35\ cm & 345 \\
	\hline
	10 & Pendelt Von 5 \ cm auf 35\ cm & 361 \\
	\hline

\end{tabularx}	

\end{document}

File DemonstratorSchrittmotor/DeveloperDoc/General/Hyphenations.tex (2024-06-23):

%%%%%%%%%%%%%%%%%%%%%%%%%%%%%%
%
% $Autor: Wings $
% $Datum: 2019-12-09 11:50:02Z $
% $Pfad: DemonstratorSchrittmotor\DeleoperDoc\General\Hyphenations.tex $
% $Version: 1766 $
%
%
%%%%%%%%%%%%%%%%%%%%%%%%%%%%%%

\usepackage[babel]{microtype}
\hyphenchar\font=\string"7F

\hyphenation{De-na-vit-Har-ten-berg-Kon-ven-tion}
\hyphenation{De-na-vit-Har-ten-berg-Dar-stel-lung}
\hyphenation{De-na-vit-Har-ten-berg-Pa-ra-me-ter}
\hyphenation{Fließ-kom-ma-a-ri-thme-tik}
\hyphenation{ent-we-der}

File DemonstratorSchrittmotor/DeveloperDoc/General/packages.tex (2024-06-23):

%%%%%%%%%%%%%%%%%%%%%%%%%%%%%%
%
% $Autor: Wings $
% $Datum: 2020-01-30 07:43:10Z $
% $Pfad: DemonstratorSchrittmotor\DeleoperDoc\General\packages.tex $
% $Version: 1786 $
%
%
%%%%%%%%%%%%%%%%%%%%%%%%%%%%%%

\usepackage[left=4cm,right=4cm,top=2cm,bottom=2cm,includeheadfoot]{geometry}
\setlength{\headheight}{1pt}

% Standard Deutsch
\usepackage{lmodern}
\usepackage[utf8]{inputenc}
\ifdefined\isGerman
  \usepackage[ngerman]{babel}
\else
  \ifdefined\isEnglish
    \usepackage[english]{babel}
  \else
    \usepackage[ngerman]{babel}
  \fi
\fi

\usepackage[T1]{fontenc}

% Farben
\usepackage{xcolor}
\usepackage{alltt}
% Notwendig für Syntax-Highlighting mit besonderen Farben
%\usepackage[table, x11names]{xcolor}
\usepackage{color}
\usepackage{soul}

% Pakete für Mathe
\usepackage{amsmath}
\usepackage{amsfonts}
\usepackage{amssymb}
\usepackage{mathtools}

% Paket Internetrefferenzen
\usepackage{hyperref}

%Wird zusätzlich das Paket showidx eingebunden, werden die gesetzten Einträge am Seitenrand dargestellt. 
\usepackage{imakeidx}
%\usepackage{showidx}
%\usepackage[override=false]{seealso}
\makeindex[intoc,title=Index]
\ifdefined\isGerman
  \renewcommand{\indexname}{Stichwortverzeichnis}
\else
\ifdefined\isEnglish
\else
  \renewcommand{\indexname}{Stichwortverzeichnis}
\fi
\fi

% Paktete für Bilder
\usepackage{graphicx}
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

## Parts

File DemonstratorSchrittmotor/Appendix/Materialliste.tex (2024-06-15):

%%%%%%%%%%%%%%%%%%%%
%
% $Beschreibung: Materialliste $
% $Autor: Theilmann $
% $Datum:  11.06.2024 $
% $Pfad: DemonstratorSchrittmotor/DeveloperDoc/Appendix/Materialliste.tex $
% $Version: 4 $
%
%
%%%%%%%%%%%%%%%%%%%

\chapter{Materialliste} \label{MLL}
\begin{center}
	\fontsize{8}{10}\selectfont
	\begin{tabularx}{\linewidth}{|p{0.4cm}|p{0.4cm}|X|X|p{1cm}|X|X|}
		\hline 
		\textbf{Pos.} & \textbf{Stk.} & \textbf{Bezeichnung} & \textbf{Artikel-Nr.}& \textbf{Preis[€]} & \textbf{Abbildung} & \textbf{Bestelladresse} \\ \hline
		1 & 1 & Arduino Lern-Kit: & ARD KIT TINYML & 52,40 & 
			
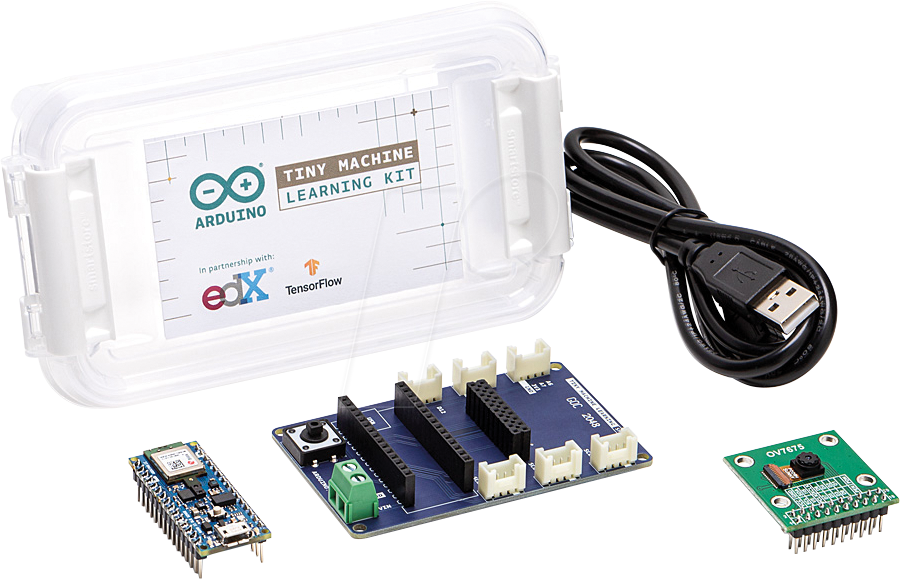
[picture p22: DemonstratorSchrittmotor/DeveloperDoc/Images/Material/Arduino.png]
  	  & \href{https://www.reichelt.de/sg/de/arduino-lern-kit-tiny-machine-ard-kit-tinyml-p304338.html}{www.reichelt.de} \\
		&   & - Arduino Nano Sense BLE 33 BLE Lite & & & \\ 
		&   &- USB-A-Micro Verbindungskabel & & & \\
		&   &- Klemmboard & & & \\
		\hline
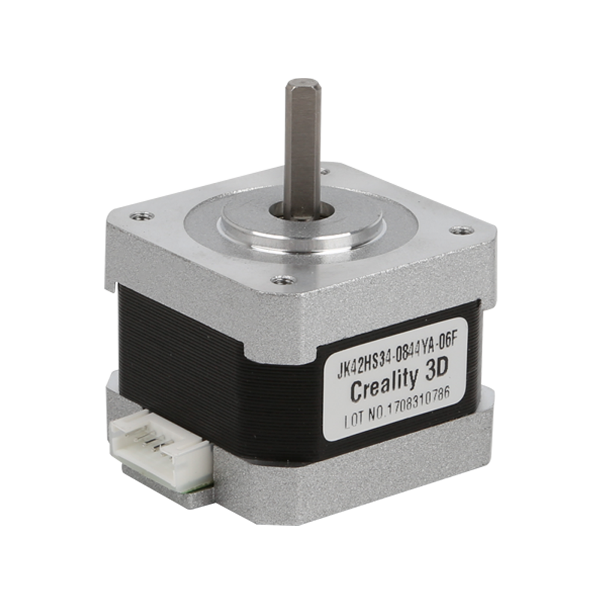
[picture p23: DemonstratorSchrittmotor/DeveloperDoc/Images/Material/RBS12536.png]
		2 & 1 & CR-10 Nema 17 Schrittmotor 34\ mm 42-34 & RBS12536 & 14,25  &  & \href{https://www.roboter-bausatz.de/p/cr-10-nema-17-schrittmotor-34mm-42-34}{www.roboter-bausatz.de} \\
		\hline
		
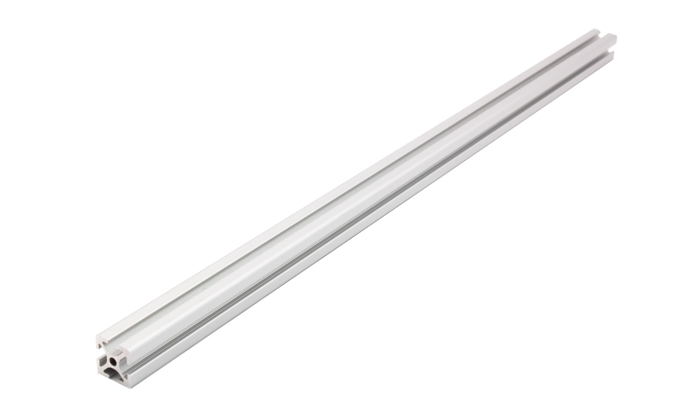
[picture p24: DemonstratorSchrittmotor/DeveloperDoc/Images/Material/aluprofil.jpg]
		3 & 1 & 1\ m Aluprofil $20 \times 20$ I-Typ Nut 5 & RBS12105 & 11,81  &  & \href{https://www.roboter-bausatz.de/p/1-meter-aluprofil-20x20-i-typ-nut-5}{www.roboter-bausatz.de} \\ 
		\hline
		4 & 1 & Schaltnetzteil, geschlossen, 50\ W, 5/12\ V, 6\ A & SNT RD 50A
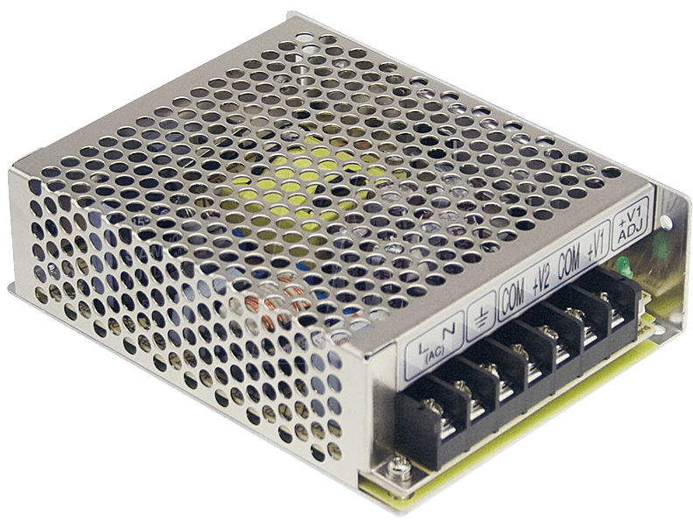
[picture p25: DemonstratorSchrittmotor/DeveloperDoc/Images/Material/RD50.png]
		& 17,10   &  & \href{https://www.reichelt.de/sg/de/schaltnetzteil-geschlossen-50-w-5-12-v-6-a-snt-rd-50a-p137098.html}{www.reichelt.de} \\ 
		\hline
		5 & 1 & Mini Spannungsregler Step-Down Modul AMS1117 3,3 VV AMS1117
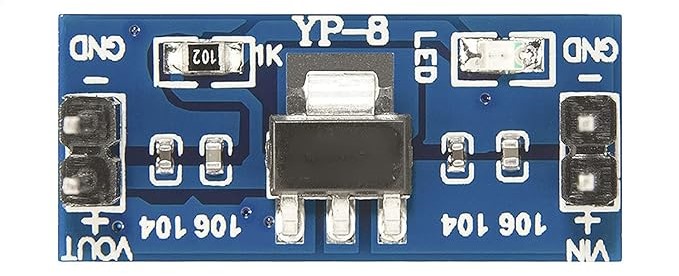
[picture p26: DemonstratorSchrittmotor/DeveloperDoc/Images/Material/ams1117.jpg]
		& RBS10505 & 0,65   &  & \href{https://www.roboter-bausatz.de/p/mini-spannungsregler-step-down-modul-ams1117-3-3-v}{www.roboter-bausatz.de} \\ 
		\hline
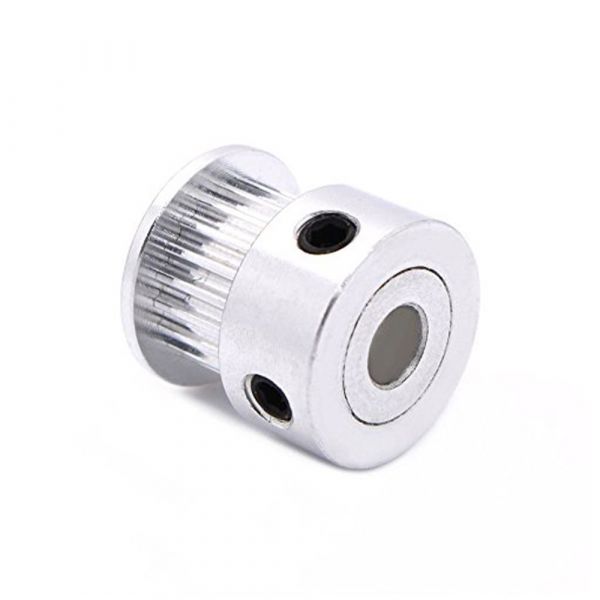
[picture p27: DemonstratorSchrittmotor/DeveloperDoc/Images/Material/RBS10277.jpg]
		6 & 1 & GT2 Riemenscheibe 20 Zähne 5\ mm Bohrung für 6\ mm Riemen & RBS10277 & 1,10  &  & \href{https://www.roboter-bausatz.de/p/gt2-riemenscheibe-20-zaehne-5mm-bohrung-fuer-6mm-riemen}{www.roboter-bausatz.de} \\ 
		\hline
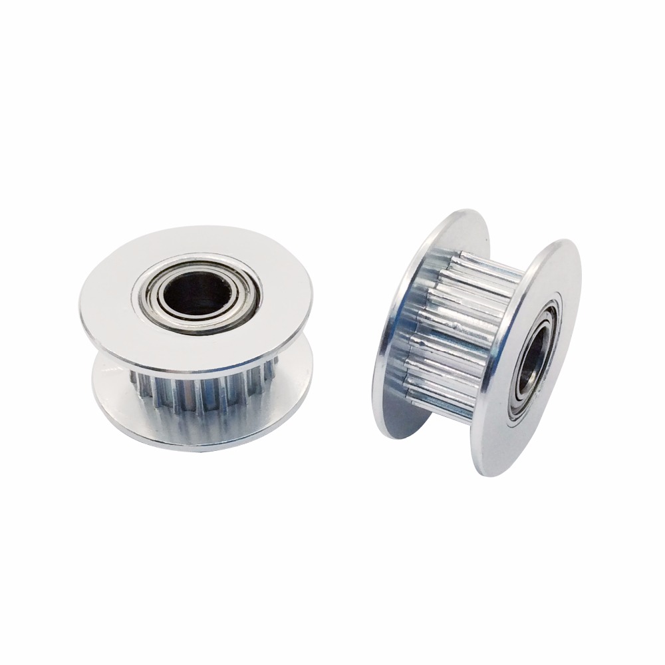
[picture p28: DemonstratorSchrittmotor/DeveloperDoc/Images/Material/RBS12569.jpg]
		7 & 1 & GT2 Riemenscheibe 20 Zähne 5\ mm Bohrung mit Dual Kugellager & RBS12569 & 1,85   &  &	\href{https://www.roboter-bausatz.de/p/gt2-riemenscheibe-20-zaehne-5mm-bohrung-mit-dual-kugellager}{www.roboter-bausatz.de} \\ 
		\hline
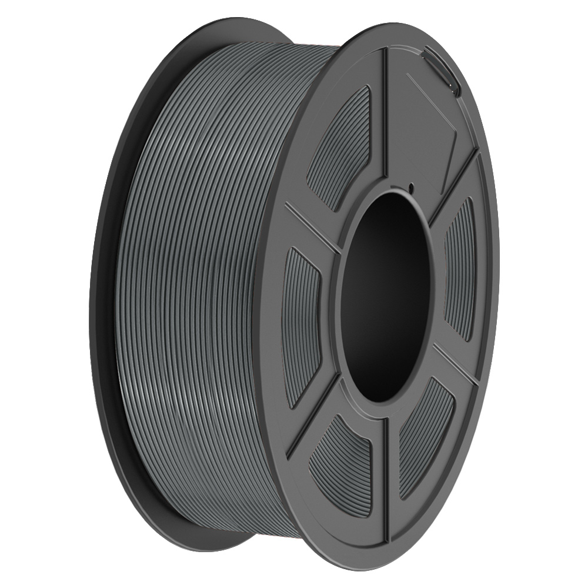
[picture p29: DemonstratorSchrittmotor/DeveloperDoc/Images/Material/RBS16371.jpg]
		8 & 0,5 &yourDroid High Speed PLA Grau 1.75mm 1 \ kg  & RBS16371 & 16,95   &  & \href{https://www.roboter-bausatz.de/p/yourdroid-high-speed-pla-grau-1.75mm-1kg}{www.roboter-bausatz.de} \\ 
		\hline		
				\end{tabularx}
		
		\fontsize{8}{10}\selectfont
		\begin{tabularx}{\textwidth}{|p{0.4cm}|p{0.4cm}|X|X|p{1cm}|X|X|}
		\hline 
		\textbf{Pos.} & \textbf{Stk.} & \textbf{Bezeichnung} & \textbf{Artikel-Nr.}& \textbf{Preis[€]} & \textbf{Abbildung} & \textbf{Bestelladresse} \\ \hline	
		9 & 1 & Linearführung MGN12H 450\ mm & RBS12916 & 29,21  &   & \href{https://www.roboter-bausatz.de/p/linearfuehrung-mgn12h-450mm}{www.roboter-bausatz.de} \\
		\hline			
		10 & 1 & yourDroid GT2 Zahnriemen offen; 6\ mm; 1\ m faserverstärkt & RBS10161 & 2,25  &  & \href{https://www.roboter-bausatz.de/p/yourdroid-gt2-zahnriemen-offen-6mm-1-meter-faserverstaerkt}{www.roboter-bausatz.de} \\
		\hline
		11 & 17 & M3 Hammermutter T-Schlitz Nut 6 &  RBS11229 & 0,29   &  & \href{https://www.roboter-bausatz.de/p/m3-hammermutter-t-schlitz-nut-6}{www.roboter-bausatz.de} \\
		\hline
		12 & 14 & Zylinder-schrauben M3 6 mm Innensechskant DIN 912 Edelstahl & 888735 & 0,18  &  &
		\href{https://www.conrad.de/de/p/toolcraft-888735-zylinderschrauben-m3-6-mm-innensechskant-din-912-edelstahl-a2-1-st-888735.html}{www.conrad.de} \\
		\hline
		13 & 6 & Zylinder-schrauben M3 8 mm Innensechskant DIN 912 Edelstahl & 827278 & 0,18  &  &
		\href{https://www.conrad.de/de/p/toolcraft-827278-zylinderschrauben-m3-8-mm-innensechskant-din-912-stahl-8-8-geschwaerzt-1-st-827278.html}{www.conrad.de} \\
		\hline
		14 & 21 & Zylinder-schrauben M3 10 mm Innensechskant DIN 912 Edelstahl & 888738 & 0,10  &  &
		\href{https://www.conrad.de/de/p/toolcraft-888738-zylinderschrauben-m3-10-mm-innensechskant-din-912-edelstahl-a2-1-st-888738.html}{www.conrad.de} \\
		\hline
		15 & 7 & Zylinder-schrauben M3 14 mm Innensechskant DIN 912 Edelstahl A2 100 St. & 1061821 & 0,18  &  &
		\href{https://www.conrad.de/de/p/toolcraft-1061821-zylinderschrauben-m3-14-mm-innensechskant-din-912-edelstahl-a2-100-st-1061821.html}{www.conrad.de} \\
		\hline
		16 & 7 & Sechskant-muttern M3 DIN 934 Stahl verzinkt & 888718  & 0,02 &  &
		\href{https://www.conrad.de/de/p/toolcraft-888718-sechskantmuttern-m3-din-934-stahl-verzinkt-1-st-888718.html}{www.conrad.de} \\
		\hline
		17 & 2 & Senkschrauben M2.5 5 mm Kreuzschlitz Phillips DIN 965 Stahl verzinkt & 889754 & 0,06  &  &
		\href{https://www.conrad.de/de/p/toolcraft-889754-senkschrauben-m2-5-5-mm-kreuzschlitz-phillips-din-965-stahl-verzinkt-1-st-889754.html}{www.conrad.de} \\
		\hline
	
			\end{tabularx}
		
		\fontsize{8}{10}\selectfont
		\begin{tabularx}{\textwidth}{|p{0.4cm}|p{0.4cm}|X|X|p{1cm}|X|X|}
		\hline 
		\textbf{Pos.} & \textbf{Stk.} & \textbf{Bezeichnung} & \textbf{Artikel-Nr.}& \textbf{Preis[€]} & \textbf{Abbildung} & \textbf{Bestelladresse} \\ \hline	
		18 & 1 & BMI Lineal 963050030 Maßstab 0,5 \ m Edelstahl & 823983 - 62 & 9,49  &  & \href{https://www.conrad.de/de/p/bmi-lineal-963050030-massstab-0-5-m-edelstahl-823983.html}{www.conrad.de} \\
		\hline
		19 & 1 & 65 Jumper Wire Kabel im Set & RBS10023 & 1,55  &  & \href{https://www.roboter-bausatz.de/p/65-jumper-wire-kabel-im-set}{www.roboter-bausatz.de} \\
		\hline
		20 & 8 & 40 Pin Dupont / Jumper Kabel Buchse-Buchse 20 \ cm & RBS101136 & 0,98  &  & \href{https://www.roboter-bausatz.de/p/40-pin-dupont-jumper-kabel-buchse-buchse-20-cm}{www.roboter-bausatz.de} \\
		\hline
		21 & 5 & 40 Pin Jumper Kabel Buchse-Stecker 20 \ cm &  RBS10038 & 1,15  &  & \href{https://www.roboter-bausatz.de/p/40-pin-jumper-kabel-buchse-stecker-20-cm}{www.roboter-bausatz.de} \\
		\hline
		22 & 2 & Arduino - Grove Universal-Kabel, 4-Pin, 20 \ cm &  GRV CABLE4PIN20 & 3,50  &  & \href{https://www.reichelt.de/arduino-grove-universal-kabel-4-pin-20cm-5er-pack--grv-cable4pin20-p191148.html}{www.reichelt.de} \\
		\hline
		23 & 1 & Schrittmotor-kabel 4 Pin auf 6 Pin HX2.54 50 \ cm & RBS10966 & 0,98  &  & \href{https://www.roboter-bausatz.de/p/schrittmotorkabel-4-pin-auf-6-pin-hx2.54-50-cm}{www.reichelt.de} \\
		\hline
		24 & 9 & Ring-Kerbschuhe, für M4, blau &  VT RK-B-4 & 0,13 &  & \href{https://www.reichelt.de/ring-kerbschuhe-fuer-m4-blau-vt-rk-b-4-p231385.html}{www.reichelt.de} \\
		\hline
		25 & 3 & Flachstecker-hülse, Breite: 4,7 \ 5mm, blau &  VT FSH-B-4,75 & 0,10 &  & \href{https://www.reichelt.de/flachsteckerhuelse-breite-4-75mm-blau-vt-fsh-b-4-75-p231336.html}{www.reichelt.de} \\
		\hline
		26 & 1 & Anschlussleitung H07RN-F, 3 x 2,5 \ mm, 10 \ m &  H07RN F325 10M & 31,40 &  & \href{https://www.reichelt.de/anschlussleitung-h07rn-f-3-x-2-5-mm-10-m-h07rn-f325-10m-p85894.html}{www.reichelt.de} \\
		\hline
		27 & 1 & Netzkabel, Schutzkontaktstecker gew, 1,8 m, schw, C13 gew & NKSK 200 SW GEW & 3,00  &  & \href{https://www.reichelt.de/sg/de/netzkabel-schutzkontaktstecker-gew-1-8-m-schw-c13-gew-nksk-200-sw-gew-p113125.html}{www.reichelt.de} \\
		\hline

			\end{tabularx}

	\fontsize{8}{10}\selectfont
	\begin{tabularx}{\textwidth}{|p{0.4cm}|p{0.4cm}|X|X|p{1cm}|X|X|}
	\hline 
	\textbf{Pos.} & \textbf{Stk.} & \textbf{Bezeichnung} & \textbf{Artikel-Nr.}& \textbf{Preis[€]} & \textbf{Abbildung} & \textbf{Bestelladresse} \\ \hline		
	28 & 2 & Hebelklemme 3-polig Ø 0,2 \ mm - 2,5 \ mm 10 Stück & 4650057 & 4,99  &  & \href{https://www.obi.de/p/4650057/hebelklemme-3-polig-0-2-mm-2-5-mm-10-stueck}{www.obi.de} \\
	\hline
	29 & 1 & Artillery Sidewinder X2 Wippschalter AC-01 & RBS15072 & 4,19  &  & \href{https://www.roboter-bausatz.de/p/artillery-sidewinder-x2-wippschalter-ac-01}{www.roboter-bausatz.de} \\
	\hline
	30 & 1 & Entwicklerboard Drehwinkel-Encoder & KY-040 & 2,20  &  & \href{https://www.reichelt.de/sg/de/entwicklerboards-drehwinkel-encoder-ky-040-debo-encoder-p282545.html}{www.reichelt.de} \\
	\hline
	31 & 1 & Kontermutter für Potentiometerknöpfe & P4-Mutter & 0,22  &  & \href{https://www.reichelt.de/sg/de/kontermutter-fuer-potentiometerknoepfe-schwarz-p4-mutter-p13757.html}{www.reichelt.de} \\
	\hline
	32 & 1 & Drucktaster Button Schalter Grün 12\ mm; 250\ V; 1\ A  & RBS13869 & 0,85  &  & \href{https://www.roboter-bausatz.de/p/drucktaster-button-schalter-gruen-12mm-250v-1a}{www.roboter-bausatz.de} \\
	\hline
	33 & 1 & Mikroschalter / Miniatur Endschalter & RBS 10856 & 0,49  &  & \href{https://www.roboter-bausatz.de/p/mikroschalter-miniatur-endschalter}{www.roboter-bausatz.de} \\
	\hline
	34 & 1 & Entwicklerboard Schrittmotorsteuerung, A4988 & DEBO DRV A4988 & 5,80  &  & \href{https://www.reichelt.de/sg/de/entwicklerboards-schrittmotorsteuerung-a4988-debo-drv-a4988-p282646.html}{www.reichelt.de} \\
	\hline
	35 & 1 & Signallleuchte, SMD-LED, ø3\ mm, Kunststoff & MEN 2660.8301 & 4,60 &  & \href{https://www.reichelt.de/sg/de/signallleuchte-smd-led-3mm-kunststoff-men-2660-8301-p366869.html}{www.reichelt.de} \\
	\hline
	36 & 1 & 0,96 Zoll OLED Display I2C/IIC/TWI 128x64 Pixel für Arduino & RBS10350 & 4,05 &  & \href{https://www.roboter-bausatz.de/p/0.96-oled-display-i2c-iic-twi-128x64-pixel-fuer-arduino}{www.roboter-bausatz.de} \\
	\hline

		\end{tabularx}
		
	\fontsize{8}{10}\selectfont
	\begin{tabularx}{\textwidth}{|p{0.4cm}|p{0.4cm}|X|X|p{1cm}|X|X|}
	\hline 
	\textbf{Pos.} & \textbf{Stk.} & \textbf{Bezeichnung} & \textbf{Artikel-Nr.}& \textbf{Preis[€]} & \textbf{Abbildung} & \textbf{Bestelladresse} \\ \hline		
	37 & 14 & Einpressmuttern $M3\times 4 \times 4$ 100 Stück für Voron 2.4 & RBS15553 & 3,14 &  & \href{https://www.roboter-bausatz.de/p/einpressmuttern-m3x4x4-100-stueck-fuer-voron-2.4}{www.roboter-bausatz.de} \\
			\hline
	38 & 0,1 & Sunlu PLA Filament Grass Green 1.75mm 1kg & RBS16624 & 17,95   &  & \href{https://www.roboter-bausatz.de/detail/index/sArticle/6689}{www.roboter-bausatz.de} \\ 
			\hline
			\end{tabularx}
				\captionof{table}{Materialliste}
				\label{Materialliste}
\end{center}

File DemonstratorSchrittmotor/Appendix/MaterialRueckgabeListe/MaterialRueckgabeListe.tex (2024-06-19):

%%%%%%%%%%%%
% $Beschreibung: Liste der zurückgegebenen Teile
% $Autor: Theilmann $
% $Datum: 19.06.2024 $
% $Pfad: DemonstratorSchrittmotor/Appendix/Rueckgabeliste/Rueckgabeliste.tex $
% $Version: 1 $
%
%%%%%%%%%%%%
\documentclass[12pt,a4paper]{scrbook}
\include{Packages}

\begin{document}

	\chapter{Materialrückgabeliste}
	
	\section{Materialliste der zurückgegeben Teile (Gruppe A24-27)}
		
\fontsize{8}{10}\selectfont
\begin{tabularx}{\textwidth}{|p{0.4cm}|p{1cm}|X|X|p{1cm}|X|}
	\hline 
	\textbf{Pos.}  & \textbf{Anzahl} & \textbf{Bezeichnung} & \textbf{Artikel-Nr.}   \\ \hline
	1 & 1 & Arduino Tiny Machine Learning Kit Box inklusive Kameramodul und USB-Kabel & ARDKITTINYML  \\
	\hline
	2 & 2 & JST- Buchsengehäuse, 1 X 4-polig - EH & JST EH4P BU  \\
	\hline
	3 & 15  & M3Hammermutter T-Schlitz Nut 6 &  RBS11229 \\
	\hline
	4 & 30 & M3 X 20 \ mm Sechskantschraube DIN912 Edelstahl & RBS14063 \\
	\hline
	5 & 23 & PinDupont/Jumper Kabel  Buchse-Buchse  & RBS101136 \\
	\hline
	6 & 2 &PinJumper Kabel Buchse-Stecker & RBS10038 \\
	\hline
	
\end{tabularx}
	
\end{document}

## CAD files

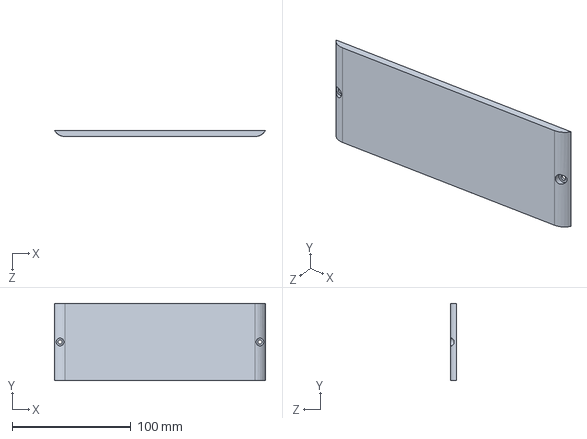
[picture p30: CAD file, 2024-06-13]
DemonstratorSchrittmotor/Appendix/Konstruktion/CADSolidWorks/WandLinks.SLDPRT
177.3 x 65.0 x 5.00 mm

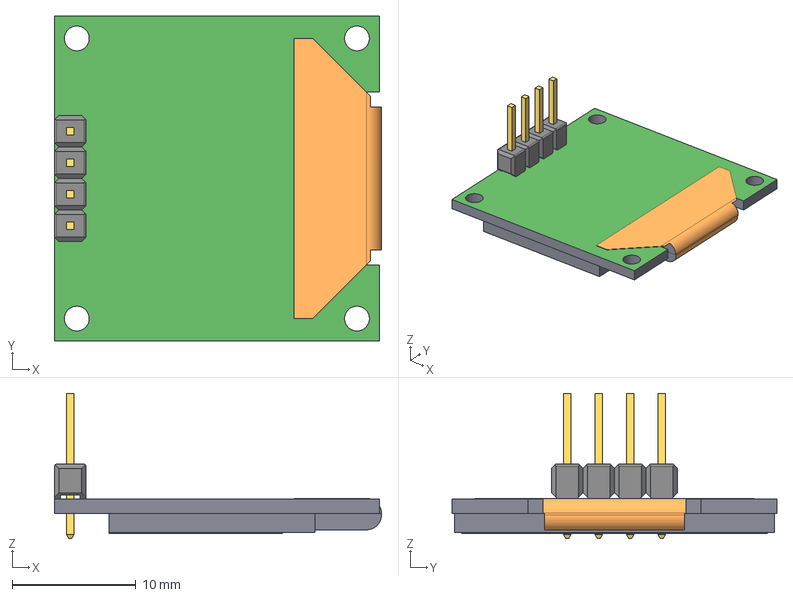
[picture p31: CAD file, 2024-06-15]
DemonstratorSchrittmotor/Appendix/Konstruktion/ExterneCAD/OLEDTEMU96in.stp
26.4 x 26.2 x 11.7 mm
brep_2 x 4

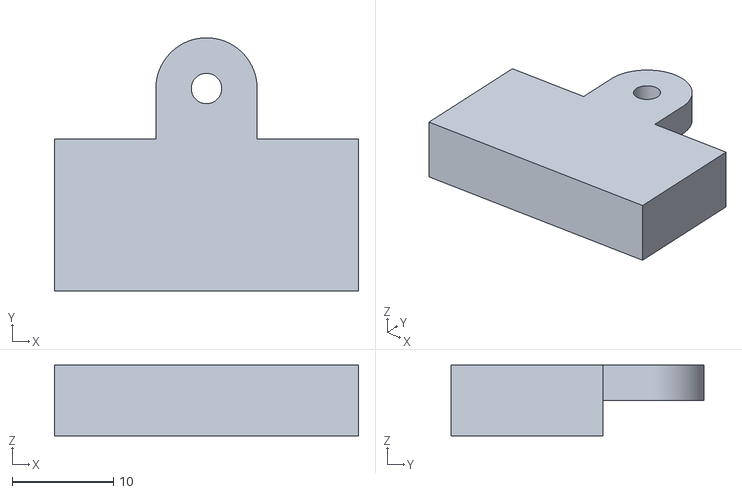
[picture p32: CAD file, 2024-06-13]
DemonstratorSchrittmotor/Appendix/Konstruktion/STL/AMS1117Halter.STL
30.0 x 25.0 x 7.00

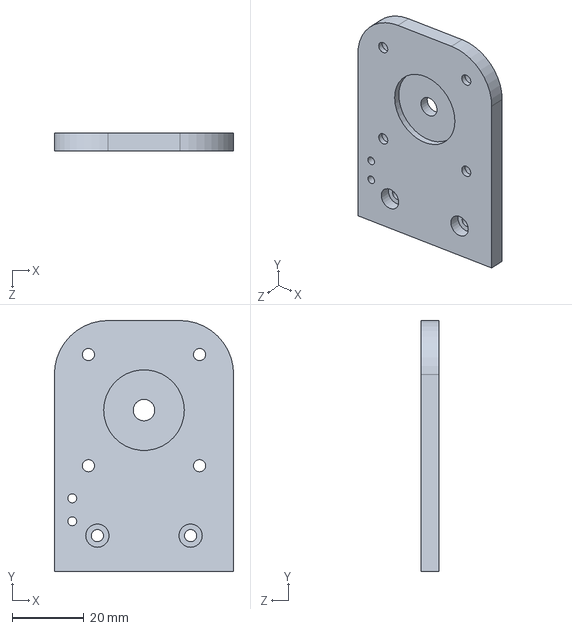
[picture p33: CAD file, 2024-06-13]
DemonstratorSchrittmotor/Appendix/Konstruktion/CADSolidWorks/FlankeMitPlatform.SLDPRT
50.0 x 70.0 x 5.00 mm

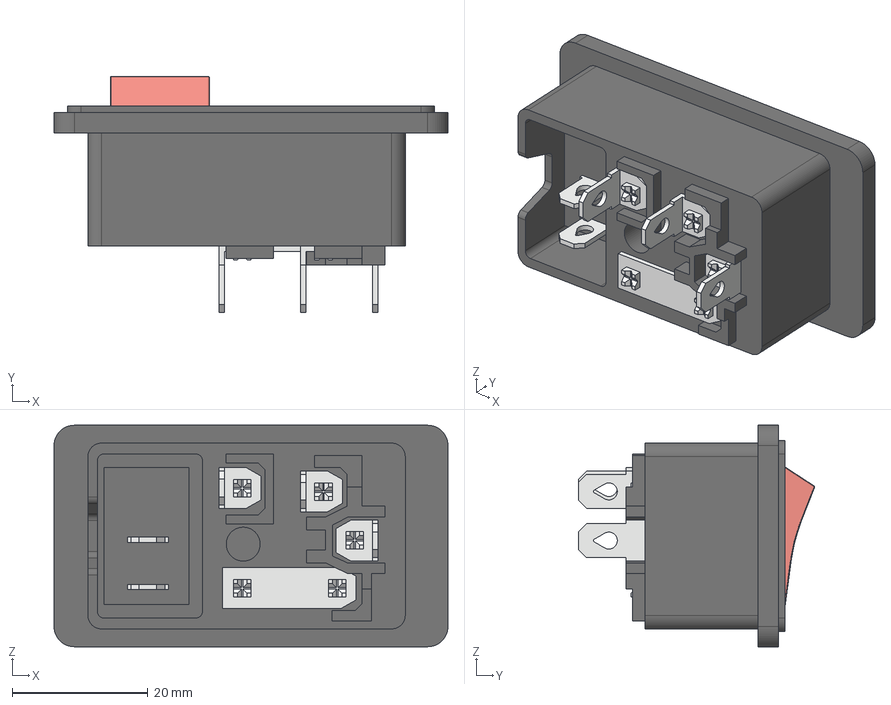
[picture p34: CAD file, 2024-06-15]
DemonstratorSchrittmotor/Appendix/Konstruktion/ExterneCAD/Kaltgeräteanschluss.stp
58.1 x 34.9 x 32.7 mm

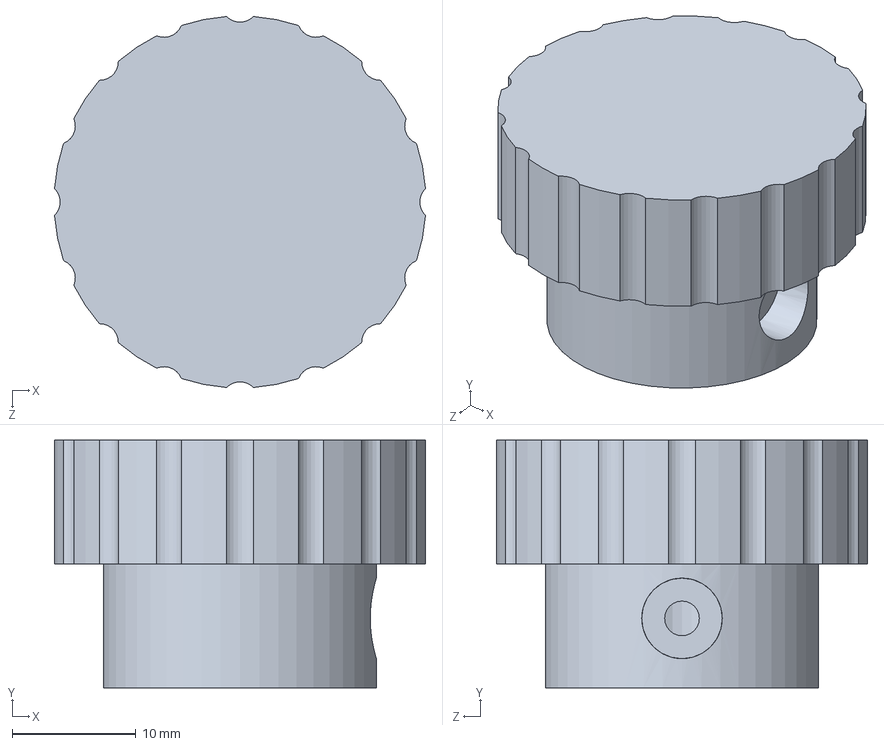
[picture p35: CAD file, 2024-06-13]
DemonstratorSchrittmotor/Appendix/Konstruktion/CADSolidWorks/Drehknopf.SLDPRT
29.9 x 20.0 x 29.9 mm

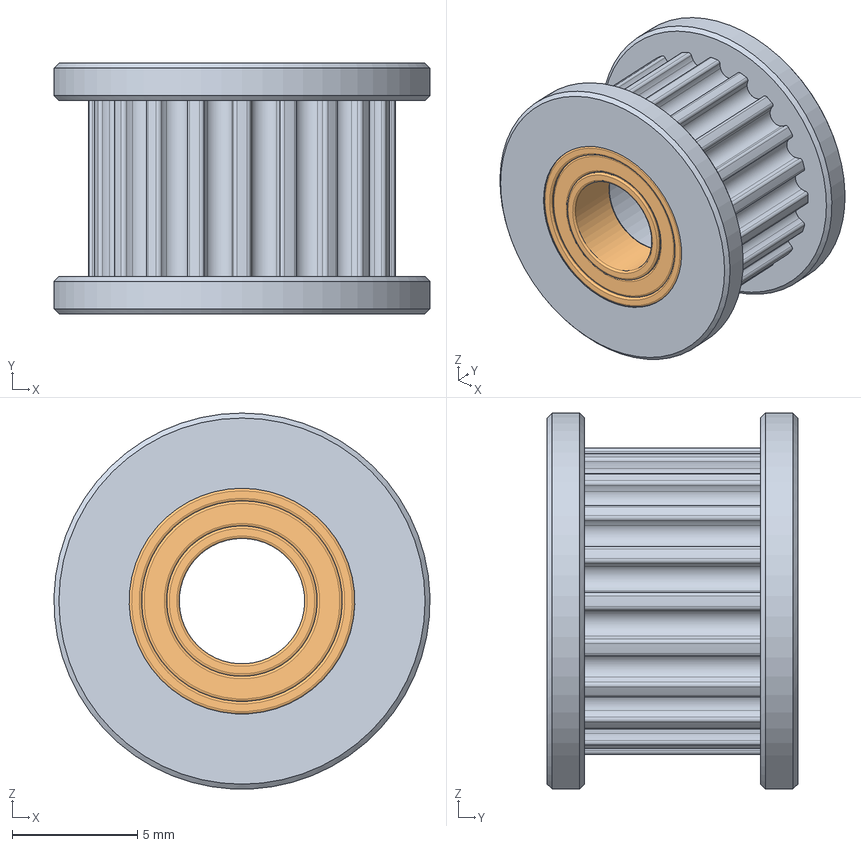
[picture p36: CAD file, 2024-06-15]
DemonstratorSchrittmotor/Appendix/Konstruktion/ExterneCAD/RiemenscheibeKugellager.step
15.0 x 10.0 x 15.0 mm
GT2_Idler_20T
Ball bearing (5x9x3)mm003
Ball bearing (5x9x3)mm004

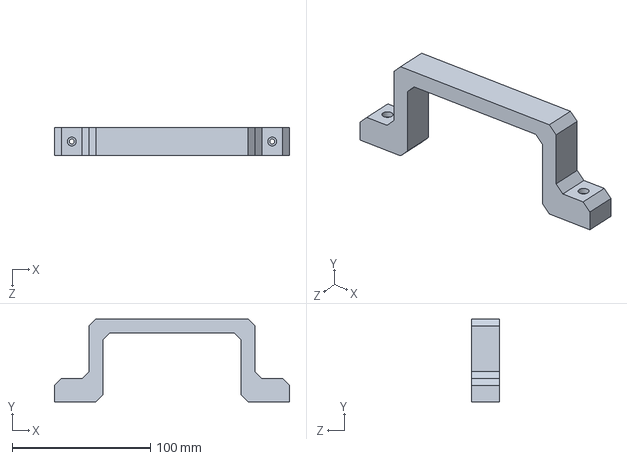
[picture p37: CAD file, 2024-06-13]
DemonstratorSchrittmotor/Appendix/Konstruktion/CADSolidWorks/Griff.SLDPRT
170.0 x 60.0 x 20.0 mm

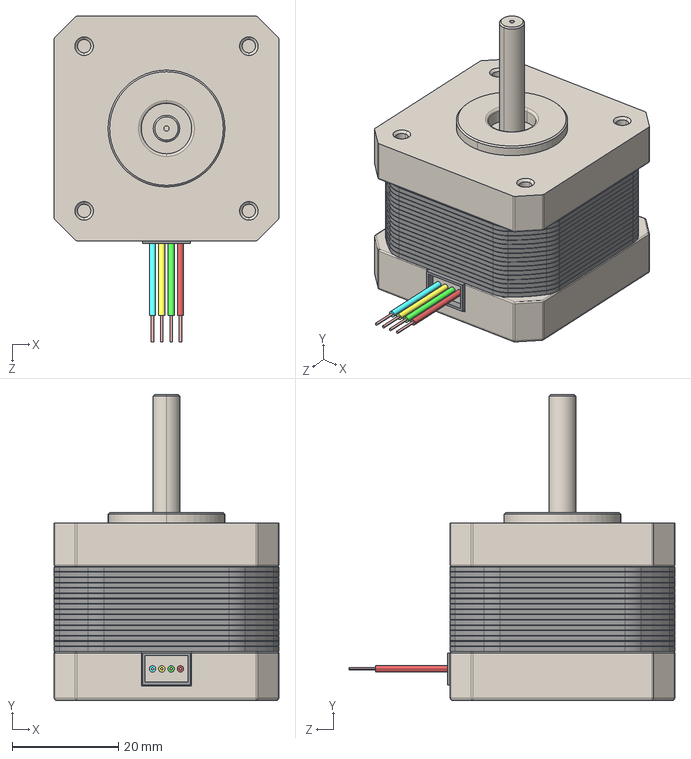
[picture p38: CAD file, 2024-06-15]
DemonstratorSchrittmotor/Appendix/Konstruktion/ExterneCAD/Nema17StepperMotorlength34mm.step
42.3 x 57.6 x 61.3 mm

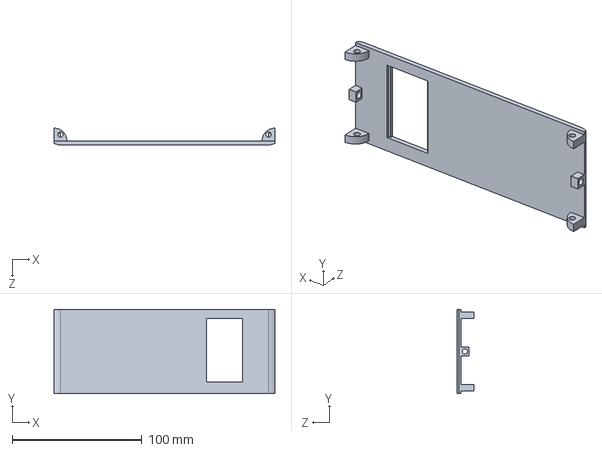
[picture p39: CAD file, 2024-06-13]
DemonstratorSchrittmotor/Appendix/Konstruktion/CADSolidWorks/Hinten.SLDPRT
170.0 x 65.0 x 13.0 mm

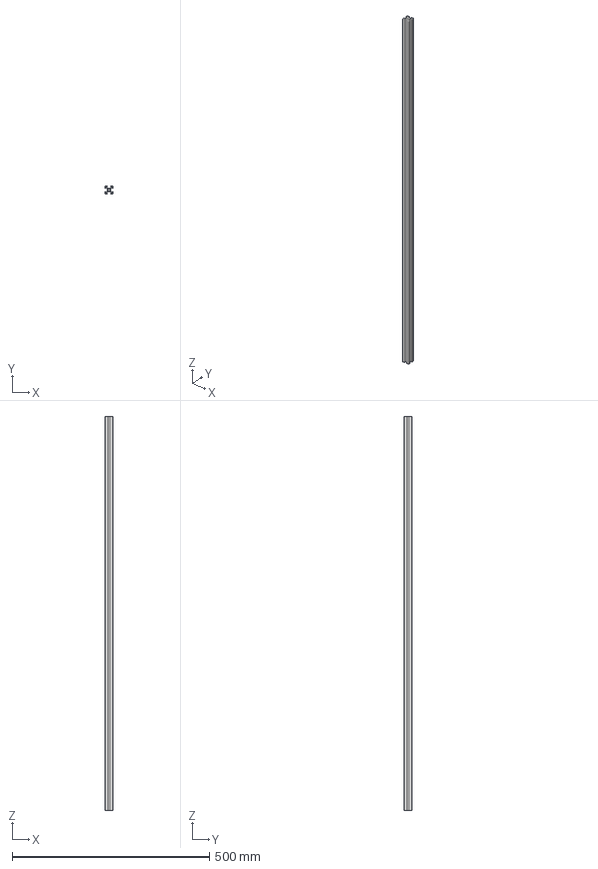
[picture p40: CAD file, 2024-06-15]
DemonstratorSchrittmotor/Appendix/Konstruktion/ExterneCAD/Aluprofil.stp
20.0 x 20.0 x 1000.0 mm

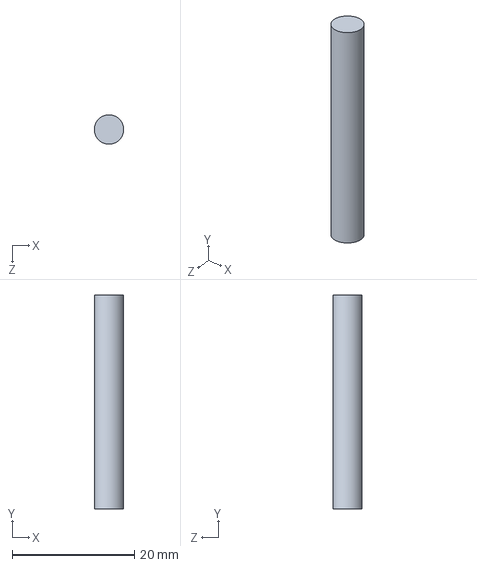
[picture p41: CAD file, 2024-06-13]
DemonstratorSchrittmotor/Appendix/Konstruktion/CADSolidWorks/Welle.SLDPRT
4.80 x 35.0 x 4.80 mm

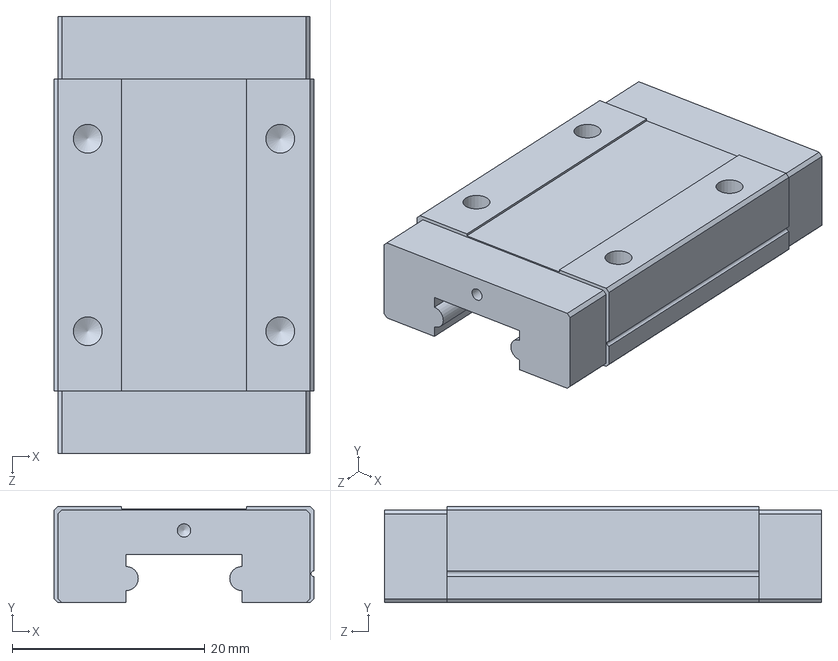
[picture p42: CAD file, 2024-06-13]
DemonstratorSchrittmotor/Appendix/Konstruktion/ExterneCAD/Schlitten.SLDPRT
27.0 x 10.0 x 45.4 mm

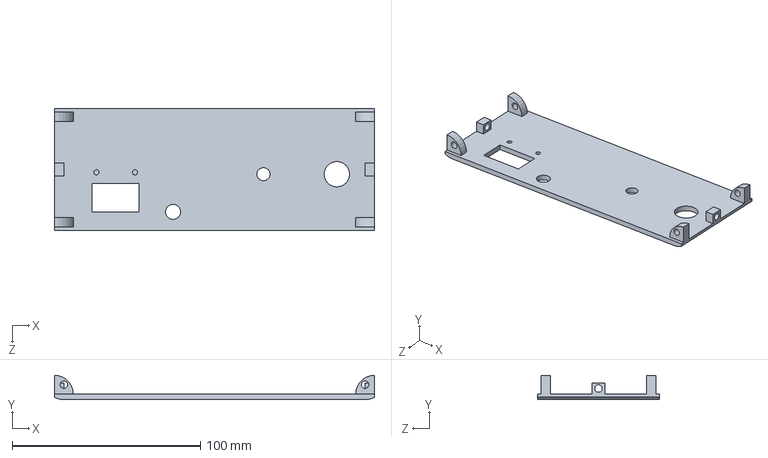
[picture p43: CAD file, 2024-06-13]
DemonstratorSchrittmotor/Appendix/Konstruktion/CADSolidWorks/Vorne.SLDPRT
170.0 x 13.0 x 65.0 mm

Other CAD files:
DemonstratorSchrittmotor/Appendix/Konstruktion/ExterneCAD/LEDgefasst3mmGrün.SLDPRT
DemonstratorSchrittmotor/Appendix/Konstruktion/CADSolidWorks/Flanke.SLDPRT
DemonstratorSchrittmotor/Appendix/Konstruktion/ExterneCAD/Druckknopf.SLDPRT
DemonstratorSchrittmotor/Appendix/Konstruktion/CADSolidWorks/Anzeiger.SLDPRT
DemonstratorSchrittmotor/Appendix/Konstruktion/CADSolidWorks/Boden.SLDPRT
DemonstratorSchrittmotor/Appendix/Konstruktion/CADSolidWorks/Deckel.SLDPRT
DemonstratorSchrittmotor/Appendix/Konstruktion/CADSolidWorks/KlipAms1117.SLDPRT
DemonstratorSchrittmotor/Appendix/Konstruktion/CADSolidWorks/WandRechts.SLDPRT
DemonstratorSchrittmotor/Appendix/Konstruktion/ExterneCAD/DruckknopfMutter.SLDPRT
DemonstratorSchrittmotor/Appendix/Konstruktion/ExterneCAD/EinpressmutterM3x4x4.SLDPRT
DemonstratorSchrittmotor/Appendix/Konstruktion/ExterneCAD/EncoderKY040.SLDPRT
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

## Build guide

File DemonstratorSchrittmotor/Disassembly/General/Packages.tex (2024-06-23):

%%%%%%
%
% $Autor: Wings $
% $Datum: 2020-01-18 11:15:45Z $
% $Pfad: DemonstratorSchrittmotor\Disassembly\Packages.tex $
% $Version: 4620 $
%
%%%%%%

\usepackage[utf8]{inputenc}
\usepackage[T1]{fontenc}

\ifdefined\isGerman
\usepackage[ngerman]{babel}
\else
\ifdefined\isEnglish
\usepackage[english]{babel}
\else
\usepackage[ngerman]{babel}
\fi
\fi

\usepackage{amsmath}
\usepackage{amsfonts}
\usepackage{amssymb}
\usepackage{graphicx}

% Paket Internetrefferenzen
\usepackage{hyperref}

\usepackage{blindtext}
\usepackage{upgreek}
\usepackage{tabularx}

\usepackage{listings}

\usepackage{enumitem,amssymb}
\newlist{todolist}{itemize}{2}
\setlist[todolist]{label=$\square$}

\usepackage{color,soul}
%\usepackage{ulem} % farbiges unterstreichen

% Farben
\usepackage{xcolor}
\usepackage{alltt,xcolor}

% Automatisches erstellen und referenzieren eines Abkürzungsverzeichnisses
\usepackage[tooltip]{acro}

\usepackage[left=2.50cm, right=2.50cm, top=2.00cm, bottom=2.00cm,
bindingoffset=8mm, includehead, includefoot]{geometry} % Loesung 8.2

\usepackage{blindtext}

\usepackage[style=ieee-alphabetic]{biblatex}

\usepackage{makeidx}
\makeindex

\usepackage[intoc]{nomencl}
\renewcommand{\nomname}{Symbolverzeichnis}
\renewcommand{\nomlabel}[1]{#1 \dotfill}
\makenomenclature

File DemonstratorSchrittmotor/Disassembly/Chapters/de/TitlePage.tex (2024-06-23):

%%%%%%
%
% $Autor: Theilmann $
% $Datum: 29.04.2024 $
% $Pfad: DemonstratorSchrittmotor\Disassembly\DemontageAnleitung.tex $
% $Version: 2 $
%
%%%%%%

\begin{titlepage}
    
    \begin{flushleft} 
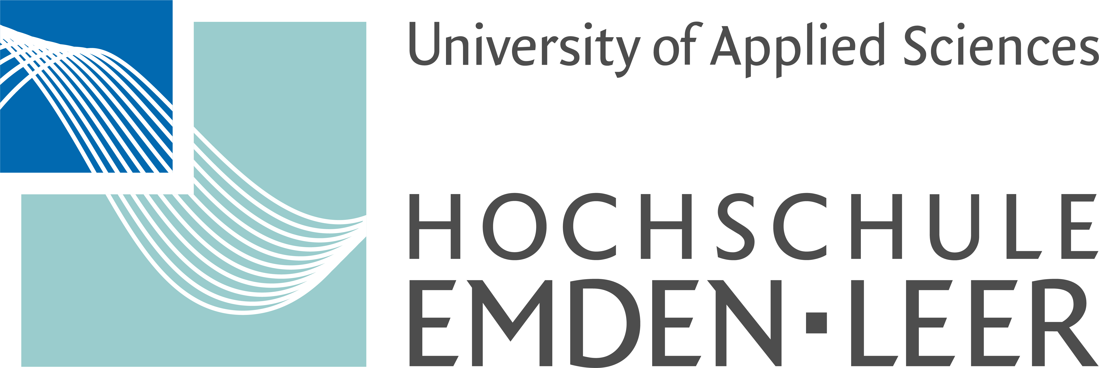
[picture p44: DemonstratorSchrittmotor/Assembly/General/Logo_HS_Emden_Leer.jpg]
        
    \end{flushleft} 
    
    \begin{flushright}
        \vspace{2cm}
        \LARGE \textsl{Demontageanleitung}\\
        \rule{0.6\textwidth}{0.4pt} ~\\
        \vspace{0.5cm}
        \textsf{\LARGE Demonstrator}\\
        \textsf{\LARGE für einen Schrittmotor}
    \end{flushright}
    
    \vspace{3cm}
    \large
    \begin{tabbing}
       xxxxxxxxxxxxxxxx \= \kill
       Autor:			\> Maik Theilmann \\
       Matrikel-Nr.:	\> 7021861 \\
       Autor:			\> Jannik Grönke \\
       Matrikel-Nr.:	\> 7022006 \\
       Autor:			\> Enno Stein \\
       Matrikel-Nr.:	\> 7021960 \\
       Autor:			\> Lars Hanneken \\
       Matrikel-Nr.:	\> 7021910 \\
       Autor:			\> Jan ter Veen \\
       Matrikel-Nr.:	\> 7022071 \\
       Studiengang: \> Maschinenbau \\ [0.5cm]
       Erstprüfer: \> Prof. Dr. Elmar Wings \\
%      Zweitprüfer: \> Prof. Dr. Max Mustermann \\ [0.5cm]
        Abgabedatum: \> \today \\
    \end{tabbing}
    
    \vspace{3cm}
    \small
    \begin{center}
        Hochschule Emden/Leer $\cdot$ 
        Fachbereich Technik $\cdot$ 
        Abteilung Maschinenbau \\
        Constantiaplatz 4 $\cdot$ 
        26723 Emden $\cdot$ 
        \url{http://www.hs-emden-leer.de}
    \end{center}
    
\end{titlepage}

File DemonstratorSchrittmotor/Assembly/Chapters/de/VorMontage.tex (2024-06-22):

%%%%%%
% $Beschreibung: Vor der Montage erledigen $
% $Autor: Theilmann $
% $Datum: 11.06.2024 $
% $Version: 1 $
% $Pfad: SchrittmotorArduino\DemonstratorSchrittmotor\Assembly\VorMontage.tex $
%
%%%%%%
\chapter{Vor der Montage}

In diesem Kapitel werden die Vorarbeiten für die Montage beschrieben. Es werden alle Bauteile, die elektrischen Komponenten, die benötigten Werkzeuge, die Vorbereitung der Leitungen und das Einsetzen der Einpressmuttern beschrieben.

\section{Bauteile}

In Abbildung \ref{Bauteile} werden alle Bauteile gezeigt und in der Tabelle \ref{BauTab} benannt.

\begin{figure}[H]
	\begin{center}
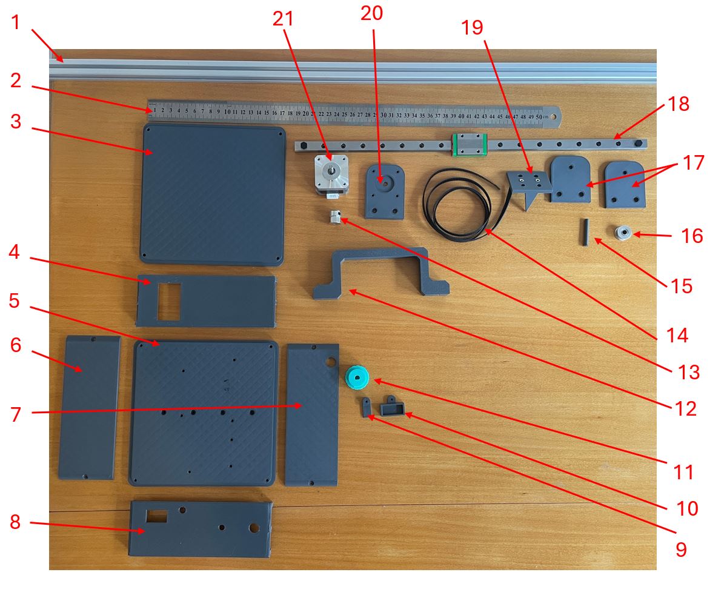
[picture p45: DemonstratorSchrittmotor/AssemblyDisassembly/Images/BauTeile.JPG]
		
		\caption{Bauteile} \label{Bauteile}
	\end{center}
\end{figure}

\begin{figure}[htp]
	\begin{center}
		\fontsize{8}{10}\selectfont
		\begin{tabularx}{\textwidth}{|p{0.4cm}|X|X|X|X|X|} 
			\hline 
			\textbf{Pos.} &  \textbf{Benennung} \\ \hline
			1 & AluProfil   \\ \hline
			2 & Linieal   \\ \hline
			3 & Deckelplatte   \\ \hline
			4 & Hinterplatte   \\ \hline
			5 & Bodenplatte   \\ \hline
			6 & Seitenplatte Links \\ \hline
			7 & Seitenplatte Rechts  \\ \hline
			8 & Vorderplatte  \\ \hline
			9 & Klipp  \\ \hline
			10 & Halter für AMS  \\ \hline
			11 & Drehknopf  \\ \hline
			12 & Transportgriff  \\ \hline
			13 & Riemenantriebsscheibe  \\ \hline
			14 & Riemen  \\ \hline
			15 & Welle  \\ \hline
			16 & Riemenscheibe  \\ \hline
			17 & Halterung für die Welle  \\ \hline
			18 & Liniearführung  \\ \hline
			19 & Anzeiger  \\ \hline
			20 & Halterung für den Motor  \\ \hline
			21 & Nema 17 Motor  \\ \hline		
				
		\end{tabularx}
		\captionof{table}{Bauteile}	\label{BauTab}
	\end{center}
\end{figure}

\section{Elektrische Komponenten}

In Abbildung \ref{Bauteile} werden alle elektrischen Komponenten dargestellt und in Tabelle \ref{ElekTab} benannt.

\begin{figure}[H]
	\begin{center}
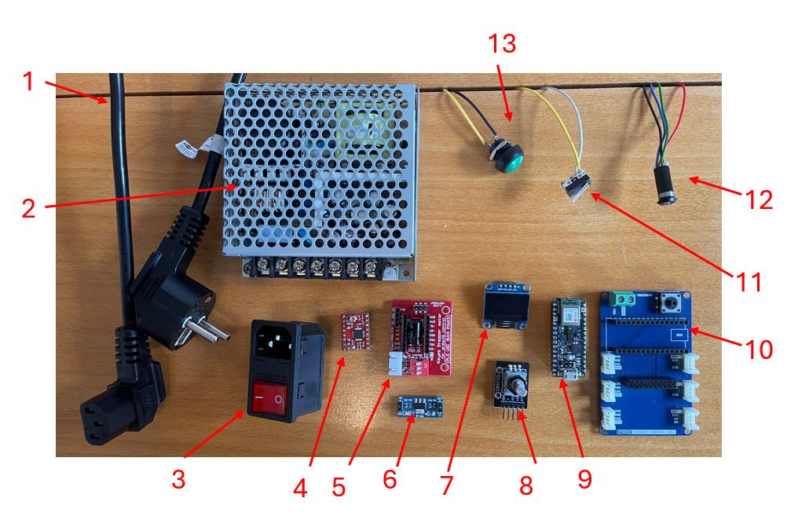
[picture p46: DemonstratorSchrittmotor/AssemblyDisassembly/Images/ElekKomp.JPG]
		
		\caption{Elektrische Komponenten} \label{ElekKomb}
	\end{center}
\end{figure}

\begin{figure}[H]
	\begin{center}
		\fontsize{8}{10}\selectfont
		\begin{tabularx}{\textwidth}{|p{0.4cm}|X|X|X|X|X|} 
			\hline 
			\textbf{Pos.} &  \textbf{Benennung} \\ \hline
			1 & Netzkabel   \\ \hline
			2 & Schaltnetzteil   \\ \hline
			3 & Kaltgeräteanschluss   \\ \hline
			4 & Schrittmotorsteuerung A4988   \\ \hline
			5 & Entwicklerboard Schrittmotorsteuerung A4988   \\ \hline
			6 & Spannungswandler AMS1117 \\ \hline
			7 & OLED-Display  \\ \hline
			8 & Drehwinkel-Encoder  \\ \hline
			9 & Arduino Nano Sense BLE 33 Lite  \\ \hline
			10 & Arduino Tiny Maschnine Learning Shield (TMLS) \\ \hline
			11 & Micro-Schalter  \\ \hline
			12 & SMD-LED \\ \hline
			13 & Drucktaster  \\ \hline
					
		\end{tabularx}
		\captionof{table}{Elektrische Komponenten}	\label{ElekTab}
	\end{center}
\end{figure}

\section{Benötigtes Werkzeug}

In der Abbildung \ref{Benwerk} sind die benötigten Werkzeuge gezeigt und in der Tabelle \ref{WerkTab} erklärt. 

\begin{figure}[H]
	\begin{center}
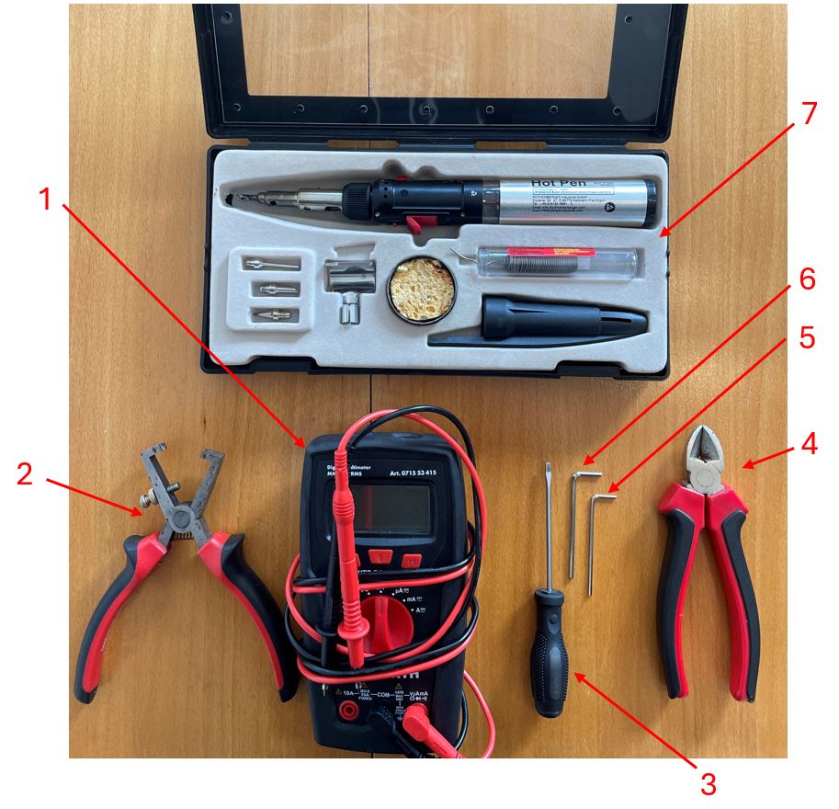
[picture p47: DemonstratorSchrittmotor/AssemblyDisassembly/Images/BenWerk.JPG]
		
		\caption{Benötigtes Werkzeug} \label{Benwerk}
	\end{center}
\end{figure}

\begin{figure}[H]
	\begin{center}
		\fontsize{8}{10}\selectfont
		\begin{tabularx}{\textwidth}{|p{0.4cm}|p{3.4cm}|X|X|X|X|} 
			\hline 
			\textbf{Pos.} &  \textbf{Benennung} &  \textbf{Beschreibung}\\ \hline
			1 & Multimeter & Vielfachmessgerät zur Messung Elektrischer Größen z.B. Spannung, Strom und Widerstand  \\ \hline
			2 & Abisolierzange & Werkzeug zum Abisolieren elektrischer Leitungen  \\ \hline
			3 & Schraubendreher Schlitz 3 \ mm & Werkzeug zum hinein- oder herausschrauben von Schrauben \\ \hline
			4 & Seitenschneider & Werkzeug zum Trennen  \\ \hline
			5 & Innensechskantschlüssel 2 \ mm &  Werkzeug zum hinein- oder herausschrauben von Schrauben \\ \hline
			6 & Innensechskantschlüssel 2.5 \ mm &  Werkzeug zum hinein- oder herausschrauben von Schrauben \\ \hline
			7 & Lötkolben &  Gerät um Bauteile zu verlöten \\ \hline

		\end{tabularx}
		\captionof{table}{Benötigtes Werkzeug}	\label{WerkTab}
	\end{center}
\end{figure}

\section{Fertigung Bauteile}

Die aus der CAD-Software konstruierten STL-Dateien müssen mit einer Slicer-Software an den jeweiligen 3D-Drucker angepasst werden. Danach können G-Codes an den 3D-Drucker exportiert und gedruckt werden. Die STL-Dateien sind unter dem Pfad zu finden: \emph{DemonstratorSchrittmotor \textbackslash Appendix \textbackslash Konstruktion \textbackslash STL}.  Wenn Sie den AnyCubic Model Kobra Neo 2 Drucker verwenden, finden Sie die fertigen G-Codes unter dem Pfad: \emph{DemonstratorSchrittmotor \textbackslash Appendix \textbackslash Konstruktion \textbackslash GCodesAnyCubicKobra2Neo}

\section{Einsetzen der Einpressmuttern}

Die Einpressmuttern werden in die Bauteile Frontplatte, Rückplatte und Anzeiger eingesetzt. In die \O 4 \ mm Bohrungen der Bauteile wird die Einpressmutter mit einem heißen Lötkolben eingepresst, bis sie bündig mit dem Bauteil abschließt. Dies ist in Abbildung \ref{Einpress} dargestellt.

\begin{figure}[H]
	\begin{center}
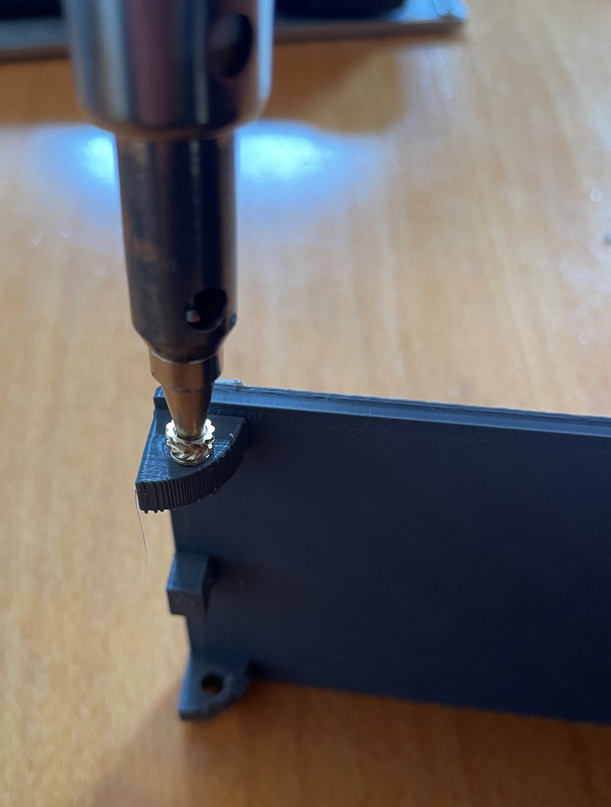
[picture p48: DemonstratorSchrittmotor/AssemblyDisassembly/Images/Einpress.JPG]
		
		\caption{Einpressen der Einpressmuttern} \label{Einpress}
	\end{center}
\end{figure}

\section{Vorbereiten der elektrischen Leitungen}

Die elektrischen Leitungen werden vor der Montage vorbereitet, um die Montage zu erleichtern. Die erforderlichen Leitungen sind in Bild \ref{Leitungen} dargestellt und in Tabelle \ref{Leittab} mit den entsprechenden Leitungsenden aufgelistet. Anschlussart, Länge und Bezeichnung sind ebenfalls angegeben.

\begin{figure}[H]
	\begin{center}
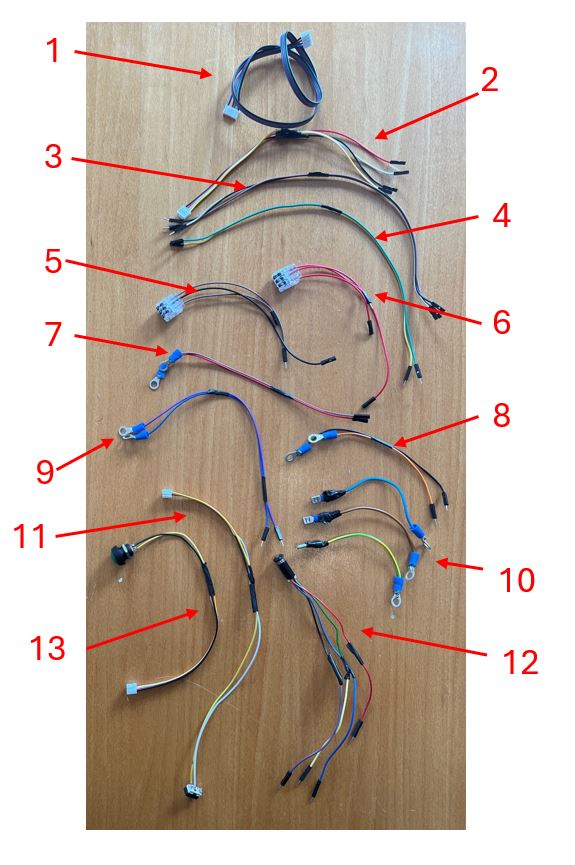
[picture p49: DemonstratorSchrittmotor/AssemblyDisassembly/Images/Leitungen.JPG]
		
		\caption{Benötigte Leitungen} \label{Leitungen}
	\end{center}
\end{figure}

\begin{figure}[H]
	\begin{center}
		\fontsize{8}{10}\selectfont
		\begin{tabularx}{\textwidth}{|p{0.5cm}|p{0.5cm}|p{2.0cm}|p{2.0cm}|p{2.0cm}|X|p{0.7cm}|X|} 
			\hline 
			\textbf{Pos.} &  \textbf{Anz.} &  \textbf{Leitungsende 1} &  \textbf{Leitungsende 2} &  \textbf{Leitungsende 3} & \textbf{Verbind-ungsart} &  \textbf{Länge [mm]} &  \textbf{Benennung} \\ \hline
			1 & 1 & 6 Pin PH2.0 & 4 Pin XH2.54 & - & - & 250 & Entwicklerboard Schrittmotorsteuerung A4988 zu Nema 17 Motor \\ \hline
			2 & 1 & 4 Pin HY2.0 & 4 x Jumper Female & - & Löten & 230 & TMLS auf OLED-Display \\ \hline
			3 & 1 & 3 x Jumper Male & 3 x Jumper Female & - & - & 320 & TMLS auf Drehwinkel-Encoder \\ \hline
			4 & 1 & 2 x Jumper Male & 2 x Jumper Female & - & - & 320 & TMLS auf Entwicklerboard Schrittmotorsteuerung A4988 \\ \hline
			5 & 1 & 1 x Jumper Male & 1 x Jumper Female & 1 x Jumper Female & Hebelklemme & 190 & Masse Spannungswandler AMS117 auf Drehwinkel-Encoder und Entwicklerboard Schrittmotorsteuerung A4988 \\ \hline
			6 & 1 & 1 x Jumper Male & 1 x Jumper Female & 1 x Jumper Female & Hebelklemme & 190 & 3,3V Spannungswandler AMS117 auf Drehwinkel-Encoder und Entwicklerboard Schrittmotorsteuerung A4988 \\ \hline
			7 & 2 & 1 x Kabelschuh Ringform & 1 x Jumper Female &  - & Quetschen & 210 & 5V/Masse Schaltnetzteil auf Spannungswandler AMS117  \\ \hline
			8 & 2 & 1 x Kabelschuh Ringform & 1 x Jumper Male &  - & Quetschen & 250 & 12V/Masse Schaltnetzteil auf Entwicklerboard Schrittmotorsteuerung A4988  \\ \hline
			9 & 2 & 1 x Kabelschuh Ringform & 1 x Jumper Male &  - & Quetschen & 170 & 12V/Masse Schaltnetzteil auf TMLS  \\ \hline
			10 & 3 & 1 x Kabelschuh Ringform & 1 x Kabelschuh Flachsteckhülse & - & 1 x Quetschen & 125 & Kaltgerätean-schluss auf Schaltnetzteil  \\ \hline
			11 & 1 & 1 x Pin HY2.0 & 2 x Micro-Schalter & - & 1 x Löten & 285 & TMLS auf Micro-Schalter  \\ \hline
			12 & 1 & 4 x Jumper Male & SMD-LED & - & Löten & 225 & TMLS auf SMD-LED  \\ \hline
			13 & 1 & 1 x Pin HY2.0 & 2 x Druckknopf x & - & Löten & 230 & TMLS auf Druckknopf  \\ \hline
			
		\end{tabularx}
		\captionof{table}{Leitungen}	\label{Leittab}
	\end{center}
\end{figure}

\section{Schrauben und Muttern }

In der folgenden Tabelle \ref{Verbrauch} werden die benötigten Schrauben und Muttern aufgelistet

\begin{figure}[H]
	\begin{center}
		\fontsize{8}{10}\selectfont
		\begin{tabularx}{\textwidth}{|p{0.5cm}|p{0,8cm}|X|X|X|X|} 
			\hline 
			\textbf{Pos.} &  \textbf{Anzahl} &  \textbf{Beschreibung}\\ \hline
			1 & 17 & M3 Hammermutter T-Schlitz Nut 6  \\ \hline
			2 & 14 & Zylinderschrauben M3 6 \ mm Innensechskant DIN 912  \\ \hline
			3 & 16 & Zylinderschrauben M3 8 \ mm Innensechskant DIN 912 \\ \hline
			4 & 21 & Zylinderschrauben M3 10 \ mm Innensechskant DIN 912\\ \hline
			5 & 7  & Zylinderschrauben M3 14 \ mm Innensechskant DIN 912 \\ \hline
			6 & 7 & Sechskantmuttern M3 DIN 934  \\ \hline
			7 & 2 &  Senkschrauben M2.5 5 \ mm Kreuzschlitz Phillips  \\ \hline
			
		\end{tabularx}
		\captionof{table}{Benötigte Schrauben und Muttern}	\label{Verbrauch}
	\end{center}
\end{figure}

\section{Schaltplan}

Der Schaltplan zeigt die elektrische Verbindung der einzelnen Komponenten. Er ist in Abbildung \ref{Splan} dargestellt.

\begin{figure}[H]
	\begin{center}
		
		\caption{Schaltplan} \label{Splan}
	\end{center}
\end{figure}

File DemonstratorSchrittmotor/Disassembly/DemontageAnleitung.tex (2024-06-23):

%%%%%%
%
% $Autor: Theilmann $
% $Datum: 29.04.2024 $
% $Version: 2 $
%
%
% !TeX encoding = utf8
% !TeX root = CornerBlending
% !TeX TXS-program:bibliography = txs:///biber
%
%%%%%%

\documentclass[12pt,a4paper]{scrbook}

% Auswahl der Sprache
% Die nicht gewünschte Sprache muss auskommentiert werden:
\def\isGerman{1}
%\def\isEnglish{1}

\include{General/Packages}
\include{General/commands}
\include{General/tikzdefs}

\input{General/acronyms}
\input{General/Hyphenations}%

\addbibresource{../Documents/literature.bib}
\addbibresource{../Documents/MyLiterature.bib}
\usepackage{float}

\begin{document}

\InputLanguage{Chapters/}{Titlepage} 
\newpage

\pagenumbering{roman}

\tableofcontents
\cleardoublepage

\addcontentsline{toc}{chapter}{\TRANS{Abbildungsverzeichnis}{List of figures}}
\listoffigures
\cleardoublepage

\addcontentsline{toc}{chapter}{\TRANS{Tabellenverzeichnis}{List of tables}}
\listoftables
\cleardoublepage

\chapter*{\TRANS{Abkürzungen}{Acronyms}}
\addcontentsline{toc}{chapter}{\TRANS{Abkürzungen}{Acronyms}}

\cleardoublepage
 
\pagenumbering{arabic}

\InputLanguage{Chapters/}{Demontage}

\cleardoublepage
\addcontentsline{toc}{chapter}{\TRANS{Literaturverzeichnis}{Bibliography}}
\printbibliography

\cleardoublepage

%\renewcommand{\indexname}{\TRANS{Stichwortverzeichnis}{Index}}
%\addcontentsline{toc}{chapter}{\TRANS{Stichwortverzeichnis}{Index}}
%\printindex

\end{document}

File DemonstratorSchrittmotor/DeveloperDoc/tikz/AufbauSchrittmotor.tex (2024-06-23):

%%%%%%
% $Beschreibung: Aufbau eines Schrittmotors $
% $Autor: ter Veen $
% $Datum: 22.06.2024 $
% $Version: 1 $
% $Pfad: SchrittmotorArduino/DevoloperDoc/tikz/AufbauSchrittmotor.tex $
%
%%%%%%

	\begin{tikzpicture}
		% stator
		\draw[thick,fill=gray!30] (0,0) circle (3.3);
		\draw[thick, fill=white] (0,0) circle (3);
		
		% Achse
		\draw[dashed] (0,3.5) -- (0,-3.5);
		
		% Polung
		\draw[thick,fill=gray!30] (-0.45,3) rectangle (0.45,2.1) node[midway] {N};
		\draw[thick,fill=gray!30] (-0.45,-3) rectangle (0.45,-2.1) node[midway] {S};
		
		\draw[thick,fill=gray!30] (3,-0.45) rectangle (2.1,0.45) node[midway] {};
		\draw[thick,fill=gray!30] (-3,-0.45) rectangle (-2.1,0.45) node[midway] {};
		
		% rotor
		\filldraw[fill=cyan!30, thick] (0,0) circle (1.5);
		\filldraw[fill=black, thick] (0,0) circle (0.5);
		
		% Spulen
		\foreach \angle in {108, -108} {
			\draw[thick] (\angle:2.65) circle (0.3);
			\node at (\angle:2.65) {\small $\bigotimes$};
		}
		
		\foreach \angle in {72, -72} {
			\draw[thick] (\angle:2.65) circle (0.3);
			\node at (\angle:2.65) {\small $\bigodot$};
		}
		
		\foreach \angle in {18, -18, 162, -162} {
			\draw[thick, fill=gray!30] (\angle:2.65) circle (0.3);
			\node at (\angle:2.65) {};
		}
		
		% labels
		\node at (0,3.8) {A1};
		\node at (0,-3.8) {A2};
		\node at (3.8,0) {B1};
		\node at (-3.8,0) {B2};
		
		\node[align=center] at (3.5,4) {Ausgeprägter Pol};
		\draw[dashed,thick] (0,2.8) -- (2,4);
		
		\node[align=center] at (3.9,3.3) {Wicklung Strang A};
		\draw[dashed,thick] (0.9,2.5) -- (2.3,3.3);
				
		\node[align=center] at (3.5,2.3) {Rotor};
		\draw[dashed,thick] (0.75,0.75) -- (3,2.3);
		
		\node[align=center] at (3.8,1.5) {Stator};
		\draw[dashed,thick] (3,0.75) -- (3.8,1.25);
		
		% Magnetfeld
		\draw[->, thick] (0.25,2.1) -- (0.25,-2.1);
		\draw[->, thick] (0,2.1) -- (0,-2.1);
		\draw[->, thick] (-0.25,2.1) -- (-0.25,-2.1);
		
		% Achse
		\draw[dashed] (3.5,0) -- (-3.5,0);
		
		 % phi
		\draw[<-, thick] (0.5,-0.5) arc[start angle=-45, end angle=135, radius=0.8] node[above left] {$\varphi$};
		
	\end{tikzpicture}

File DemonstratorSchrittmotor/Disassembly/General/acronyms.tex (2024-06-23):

%%%%%%%%%%%%%%%%%%%%%%%%%%%%%%
%
% $Autor: Wings, Reck $
% $Datum: 2020-10-12 $
% $Pfad: DemonstratorSchrittmotor\Disassembly\acronyms.tex $
% $Version: 1 $
%
%
%%%%%%%%%%%%%%%%%%%%%%%%%%%%%%

%\acsetup{
%%    list-type    = table ,
%    list-name    = Akronyme,
%    list-style   = longtable ,
%    list-heading = chapter*, % Kapitel ohne Nummerierung
%%    list-table-width = \textwidth-4\tabcolsep-6em,
%%    page-ref = dotfill , % <<< neue Instanz verwenden
%    list-short-format ={\bfseries}, % Abkürzungen in fetter Serifenschrift im Verzeichnis
%    first-long-format = {\itshape}, % Erste Lange Ausführung der Abkürzung kursiv gestellt
%}

%%%%%%%%%%%%%%%%%%%%%%%%%%%%%%%%%%%%%%%%%%%%%%%%%%%%%
% A
%%%%%%%%%%%%%%%%%%%%%%%%%%%%%%%%%%%%%%%%%%%%%%%%%%%%%

\DeclareAcronym{api}{
    short = API\index{API}, 
    long  = Application Programming Interface\index{Application Programming Interface!\Siehe {API}},
}

%%%%%%%%%%%%%%%%%%%%%%%%%%%%%%%%%%%%%%%%%%%%%%%%%%%%%
% B
%%%%%%%%%%%%%%%%%%%%%%%%%%%%%%%%%%%%%%%%%%%%%%%%%%%%%

\DeclareAcronym{bs}{
    short = BS\index{BS}, 
    long  = Batch-Size\index{Batch-Size!\Siehe {BS}},
}

%%%%%%%%%%%%%%%%%%%%%%%%%%%%%%%%%%%%%%%%%%%%%%%%%%%%%
% C
%%%%%%%%%%%%%%%%%%%%%%%%%%%%%%%%%%%%%%%%%%%%%%%%%%%%%

\DeclareAcronym{cci}{
    short = CCI\index{CCI},
    long  = Camera Control Interface\index{Camera Control Interface!\Siehe {CCI}},
}

\DeclareAcronym{csi}{
  short = CSI\index{CSI},
  long  = Camera Serial Interface\index{Camera Serial Interface!\Siehe {CSI}},
}
  
\DeclareAcronym{cg}{
    short = Cg, 
    long = C for graphics,
}

\DeclareAcronym{cifar}{
    short = CIFAR\index{Datensatz!CIFAR} ,
    long  = Canadian Institute For Advanced Research\index{Canadian Institute For Advanced Research!\Siehe {CIFAR!\Siehe {Datensatz}}},
}

\DeclareAcronym{cnc}{
    short = CNC\index{CNN} ,
    long  = Computerized Numerical Control\index{Computerized Numerical Control!\Siehe {CNN}} ,
}

\DeclareAcronym{cnn}{
    short = CNN\index{CNN} ,
    long  = Convolutional Neural Network\index{Convolutional Neural Network!\Siehe {CNN}} ,
}

\DeclareAcronym{coco}{
  short = COCO\index{COCO},
  long  = Common Objects in Context\index{Common Objects in Context!\Siehe {COCO}}
}

\DeclareAcronym{cpu}{
    short = CPU\index{CPU} ,
    long  = Central Processing Unit\index{Central Processing Unit!\Siehe {CPU}} ,
}

\DeclareAcronym{cuda}{
    short = CUDA\index{CUDA} ,
	long  = Compute Unified Device Architecture\index{Compute Unified Device Architecture!\Siehe {CUDA}} ,
}

\DeclareAcronym{cudnn}{
	short = cuDNN\index{cuDNN} ,
	long  = NVIDIA CUDA Deep Neural Network Library\index{NVIDIA CUDA Deep Neural Network Library!\Siehe {cuDNN}} ,
}

%%%%%%%%%%%%%%%%%%%%%%%%%%%%%%%%%%%%%%%%%%%%%%%%%%%%%
% D
%%%%%%%%%%%%%%%%%%%%%%%%%%%%%%%%%%%%%%%%%%%%%%%%%%%%%

\DeclareAcronym{dll}{
    short = DLL ,
    long  = Dynamic Link Library,
    long-plural-form = Dynamic Link Libraries,
}

\DeclareAcronym{dnn}{
    short = DNN ,
    long  = Deep Neural Network ,
}

%%%%%%%%%%%%%%%%%%%%%%%%%%%%%%%%%%%%%%%%%%%%%%%%%%%%%
% E
%%%%%%%%%%%%%%%%%%%%%%%%%%%%%%%%%%%%%%%%%%%%%%%%%%%%%

%%%%%%%%%%%%%%%%%%%%%%%%%%%%%%%%%%%%%%%%%%%%%%%%%%%%%
% F
%%%%%%%%%%%%%%%%%%%%%%%%%%%%%%%%%%%%%%%%%%%%%%%%%%%%%

\DeclareAcronym{fp32}{
    short = FP32, 
    long  = Floating Point 32-bit,
}

\DeclareAcronym{flops}{
    short = Flops, 
    long  = Floating Point Operations per Second - Gleitkomma­operationen pro Sekunde,
}

\DeclareAcronym{fp16}{
    short = FP16, 
    long = Floating Point 16-bit,
}

\DeclareAcronym{fpga}{
  short = FPGA,
  long  = Ffield-Programmable Gate Array,
}

\DeclareAcronym{fps}{
    short = fps,
    long  = frames per second,
}

%%%%%%%%%%%%%%%%%%%%%%%%%%%%%%%%%%%%%%%%%%%%%%%%%%%%%
% G
%%%%%%%%%%%%%%%%%%%%%%%%%%%%%%%%%%%%%%%%%%%%%%%%%%%%%

\DeclareAcronym{gpio}{
  short = GPIO\index{GPIO},
  long  = General Purpose Input Output\index{General Purpose Input Output!\Siehe GPIO},
}

\DeclareAcronym{gpgpu}{
    short = GPGPU ,
    long  = General Purpose Computation on Graphics Processing Unit\index{General Purpose Computation on Graphics Processing Unit!\Siehe GPGPU} ,
}

\DeclareAcronym{gpu}{
    short = GPU\index{GPU} ,
    long  = Graphics Processing Unit\index{Graphics Processing Unit!\Siehe GPU} ,
}

%%%%%%%%%%%%%%%%%%%%%%%%%%%%%%%%%%%%%%%%%%%%%%%%%%%%%
% H
%%%%%%%%%%%%%%%%%%%%%%%%%%%%%%%%%%%%%%%%%%%%%%%%%%%%%

\DeclareAcronym{hdmi}{
  short = HDMI\index{HDMI},
  long  = High Definition Multimedia Interface\index{High Definition Multimedia Interface!\Siehe {HDMI}},
}

%%%%%%%%%%%%%%%%%%%%%%%%%%%%%%%%%%%%%%%%%%%%%%%%%%%%%
% I
%%%%%%%%%%%%%%%%%%%%%%%%%%%%%%%%%%%%%%%%%%%%%%%%%%%%%

\DeclareAcronym{i2c}{
    short = I\textsuperscript{2}C\index{I\textsuperscript{2}C},
    long  = Inter-Integrated Circuit\index{Inter-Integrated Circuit!\Siehe I\textsuperscript{2}C},
}    

\DeclareAcronym{i2s}{
    short = I\textsuperscript{2}S\index{I\textsuperscript{2}S},
    long  = Inter-IC Sound\index{Inter-IC Sound!\Siehe I\textsuperscript{2}S},
}    

\DeclareAcronym{ide}{
	short = IDE\index{IDE} ,
	long  = Integrated Development Environment\index{Integrated Development Environment!\Siehe IDE},
}

\DeclareAcronym{int8}{
    short = INT8, 
    long = Integer 8-bit,
}

\DeclareAcronym{iot}{
    short = IoT ,
    long  = Internet of Things,
}

%%%%%%%%%%%%%%%%%%%%%%%%%%%%%%%%%%%%%%%%%%%%%%%%%%%%%
% J
%%%%%%%%%%%%%%%%%%%%%%%%%%%%%%%%%%%%%%%%%%%%%%%%%%%%%

%%%%%%%%%%%%%%%%%%%%%%%%%%%%%%%%%%%%%%%%%%%%%%%%%%%%%
% K
%%%%%%%%%%%%%%%%%%%%%%%%%%%%%%%%%%%%%%%%%%%%%%%%%%%%%

\DeclareAcronym{kdd}{
    short = KDD\index{KDD} ,
    long  = Knowledge Discovery in Databases\index{Knowledge Discovery in Databases!\Siehe KDD},
}

\DeclareAcronym{ki}{
    short = KI, 
    long  = Künstliche Intelligenz,
}

\DeclareAcronym{knn}{
    short = KNN, 
    long  = Künstliches Neuronales Netz,
}

%%%%%%%%%%%%%%%%%%%%%%%%%%%%%%%%%%%%%%%%%%%%%%%%%%%%%
% L
%%%%%%%%%%%%%%%%%%%%%%%%%%%%%%%%%%%%%%%%%%%%%%%%%%%%%

%%%%%%%%%%%%%%%%%%%%%%%%%%%%%%%%%%%%%%%%%%%%%%%%%%%%%
% M
%%%%%%%%%%%%%%%%%%%%%%%%%%%%%%%%%%%%%%%%%%%%%%%%%%%%%

\DeclareAcronym{mimd}{
    short = MIMD \index{MIND},
    long  = Multiple-Instruction Multiple-Data\index{Multiple-Instruction Multiple-Data!\Siehe MIMD} ,
}

\DeclareAcronym{nn}{
    short = NN, 
    long  = Neuronales Netz,
}

%%%%%%%%%%%%%%%%%%%%%%%%%%%%%%%%%%%%%%%%%%%%%%%%%%%%%
% N
%%%%%%%%%%%%%%%%%%%%%%%%%%%%%%%%%%%%%%%%%%%%%%%%%%%%%

%%%%%%%%%%%%%%%%%%%%%%%%%%%%%%%%%%%%%%%%%%%%%%%%%%%%%
% O
%%%%%%%%%%%%%%%%%%%%%%%%%%%%%%%%%%%%%%%%%%%%%%%%%%%%%

\DeclareAcronym{opencl}{
    short = OpenCL\index{OpenCL}, 
    long  = Open Computing Language\index{Open Computing Language!\Siehe OpenCL},
}

%%%%%%%%%%%%%%%%%%%%%%%%%%%%%%%%%%%%%%%%%%%%%%%%%%%%%
% P
%%%%%%%%%%%%%%%%%%%%%%%%%%%%%%%%%%%%%%%%%%%%%%%%%%%%%

\DeclareAcronym{ppa}{
    short = PPA\index{PPa}, 
    long  = Personal Package Archive\index{Personal Package Archive!\Siehe PPA},
}

\DeclareAcronym{pip}{
	short = pip\index{pip} ,
	long  = pip installs packages\index{pip installs packages!\Siehe pip} ,
}

\DeclareAcronym{pypi}{
	short = PyPi\index{PyPi} ,
	long  = Python Package Index\index{Python Package Index!\Siehe PyPi} ,
}

%%%%%%%%%%%%%%%%%%%%%%%%%%%%%%%%%%%%%%%%%%%%%%%%%%%%%
% Q
%%%%%%%%%%%%%%%%%%%%%%%%%%%%%%%%%%%%%%%%%%%%%%%%%%%%%

%%%%%%%%%%%%%%%%%%%%%%%%%%%%%%%%%%%%%%%%%%%%%%%%%%%%%
% R
%%%%%%%%%%%%%%%%%%%%%%%%%%%%%%%%%%%%%%%%%%%%%%%%%%%%%

\DeclareAcronym{ram}{
	short = RAM\index{RAM} ,
	long  = Random Access Memory\index{Random Access Memory! \Siehe RAM},
}

\DeclareAcronym{relu}{
    short = ReLu\index{ReLu}, 
    long  = Rectified Linear Unit\index{Rectified Linear Unit!\Siehe ReLu},
}

\DeclareAcronym{resnets}{
    short = ResNet\index{ResNet},
    long =  Residual Neural Network\index{Residual Neural Network!\Siehe ResNet},
}    

\DeclareAcronym{rle}{
    short = RLE\index{RLE},
    long  = Run-Length Encoding\index{Run-Length Encoding},
}

\DeclareAcronym{rgb}{
  short = RGB,
  long  = Rot-Grün-Blau}

%%%%%%%%%%%%%%%%%%%%%%%%%%%%%%%%%%%%%%%%%%%%%%%%%%%%%
% S
%%%%%%%%%%%%%%%%%%%%%%%%%%%%%%%%%%%%%%%%%%%%%%%%%%%%%

\DeclareAcronym{sd}{
  short = SD\index{SD},
  long  = Secure Digital\index{Secure Digital!\Siehe SD},
}

\DeclareAcronym{sda}{
    short = SDA\index{SDA},
    long  = Serial Data\index{Serial Data!\Siehe SDA},
}    

\DeclareAcronym{sd-1}{
    short = SD-1\index{Datensatz!NIST~Special~Database~1},
    long  = NIST Special Database~1\index{NIST Special Database 1!\Siehe Datensatz},
}    

\DeclareAcronym{sd-3}{
    short = SD-3\index{Datensatz!NIST Special Database 3},
    long  = NIST Special Database 3\index{NIST Special Database 3!\Siehe Datensatz},
}    

\DeclareAcronym{scl}{
    short = SCL\index{SCL},
    long  = Serial Clock\index{Serial Clock!\Siehe SCL},
}    

\DeclareAcronym{ssh}{
    short = SSH\index{SSH},
    long  = Secure Shell\index{Secure Shell!\Siehe SSH},
}

\DeclareAcronym{spi}{
    short = SPI\index{SPI},
    long  = Serial Peripheral Interface\index{Serial Peripheral Interface!\Siehe SPI},
}

\DeclareAcronym{sbc}{
    short = SBC\index{SBC} ,
    long  = Single-Board-Computer\index{Single-Board-Computer!\Siehe SBC} ,
}

\DeclareAcronym{simd}{
	short = SIMD\index{SIMD} ,
	long  = Single-Instruction Multiple-Data\index{Single-Instruction Multiple-Data!\Siehe SIMD} ,
}

\DeclareAcronym{sm}{
	short = SM\index{SM} ,
	long  = Streaming Multiprocessor\index{Streaming Multiprocessor!\Siehe SM} ,
}

\DeclareAcronym{sp}{
	short = SP\index{SP} ,
	long  = Streaming Processor\index{Streaming Processor!\Siehe SP} ,
}

\DeclareAcronym{sps}{
    short = SPS\index{SPS} ,
    long  = Speicherprogrammierbare Steuerung\index{Speicherprogrammierbare Steuerung!\Siehe SPS} ,
}

%%%%%%%%%%%%%%%%%%%%%%%%%%%%%%%%%%%%%%%%%%%%%%%%%%%%%
% T
%%%%%%%%%%%%%%%%%%%%%%%%%%%%%%%%%%%%%%%%%%%%%%%%%%%%%

\DeclareAcronym{tpu}{
	short = TPU\index{TPU}, 
	long  = Tensor Processing Unit\index{Tensor Processing Unit!\Siehe TPU},
}

%%%%%%%%%%%%%%%%%%%%%%%%%%%%%%%%%%%%%%%%%%%%%%%%%%%%%
% U
%%%%%%%%%%%%%%%%%%%%%%%%%%%%%%%%%%%%%%%%%%%%%%%%%%%%%

\DeclareAcronym{uart}{
    short = UART\index{UART}, 
    long  = Universal Asynchronous Receiver Transmitter\index{Universal Asynchronous Receiver Transmitter!\Siehe UART},
}

\DeclareAcronym{uma}{
  short = UMA\index{UMA}, 
  long  = Unified Memory Architecture\index{Unified Memory Architecture!\Siehe UMA},
}

%%%%%%%%%%%%%%%%%%%%%%%%%%%%%%%%%%%%%%%%%%%%%%%%%%%%%
% V
%%%%%%%%%%%%%%%%%%%%%%%%%%%%%%%%%%%%%%%%%%%%%%%%%%%%%

\DeclareAcronym{venv}{
    short = VENV\index{VENV} ,
    long  = Virtual Environment\index{Virtual Environment!\Siehe VENV} ,
}

\DeclareAcronym{vpu}{
  short = VPU\index{VPU},
  long  = Video Processing Unit\index{Video Processing Unit!\Siehe VPU},
}
  
%%%%%%%%%%%%%%%%%%%%%%%%%%%%%%%%%%%%%%%%%%%%%%%%%%%%%
% W
%%%%%%%%%%%%%%%%%%%%%%%%%%%%%%%%%%%%%%%%%%%%%%%%%%%%%

%%%%%%%%%%%%%%%%%%%%%%%%%%%%%%%%%%%%%%%%%%%%%%%%%%%%%
% X
%%%%%%%%%%%%%%%%%%%%%%%%%%%%%%%%%%%%%%%%%%%%%%%%%%%%%
%%%%%%%%%%%%%%%%%%%%%%%%%%%%%%%%%%%%%%%%%%%%%%%%%%%%%
% Y
%%%%%%%%%%%%%%%%%%%%%%%%%%%%%%%%%%%%%%%%%%%%%%%%%%%%%
%%%%%%%%%%%%%%%%%%%%%%%%%%%%%%%%%%%%%%%%%%%%%%%%%%%%%
% Z
%%%%%%%%%%%%%%%%%%%%%%%%%%%%%%%%%%%%%%%%%%%%%%%%%%%%%

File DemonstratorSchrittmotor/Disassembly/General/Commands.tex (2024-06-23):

%%%%%%
%
% $Autor: Wings $
% $Datum: 2020-01-18 11:15:45Z $
% $Pfad: DemonstratorSchrittmotor\Disassembly\Command.tex $
% $Version: 4620 $
%
%%%%%%

\definecolor{MapleColor}{rgb}{1,0.0,0.}
\definecolor{PythonColor}{rgb}{0,0.5,1.}
\definecolor{ShellColor}{rgb}{1,0,0.5}
\definecolor{FileColor}{rgb}{0.5,0.5,1.}

\newcommand{\MapleCommand}[1]{\textcolor{MapleColor}{\texttt{#1}}}
\newcommand{\PYTHON}[1]{\textcolor{PythonColor}{\texttt{\justify#1}}}
\newcommand{\SHELL}[1]{#1}%\textcolor{ShellColor}{\texttt{\justify#1}}}
\newcommand{\FILE}[1]{\textcolor{FileColor}{\texttt{\justify#1}}}

\newcommand{\QUELLE}{\textcolor{red}{hier Quelle finden}}

\newcolumntype{L}[1]{>{\raggedright\arraybackslash}p{#1}} % linksbündig mit Breitenangabe

\newcommand{\GRAFIK}{\textcolor{red}{Grafik einfügen}}

\newcommand{\DEF}[1]{\fcolorbox{blue}{blue!10}{\begin{minipage}{\textwidth}\textbf{Definition.}#1\end{minipage}}}

\newcommand{\BEISPIEL}[1]{\fcolorbox{blue}{blue!10}{\begin{minipage}{\textwidth}\textbf{Beispiel.}#1\end{minipage}}}

\newcommand{\SATZ}[1]{\fcolorbox{blue}{blue!10}{\begin{minipage}{\textwidth}\textbf{Satz.}#1\end{minipage}}}

\newcommand{\Bemerkung}[1]{\fcolorbox{blue}{blue!10}{\begin{minipage}{\textwidth}\textbf{Bemerkung.}#1\end{minipage}}}

\newcommand{\Po}{\mathbb{P}}
\newcommand{\R}{\mathbb{R}}

\DeclareMathOperator{\Atan2}{Atan2}
\DeclareMathOperator{\sign}{sign}

% Auswahl der Sprache
% 1.Argument ist der Pfad ohne "en" oder "de"
% 2.Argument ist der Dateiname
\newcommand{\InputLanguage}[2]{
    \ifdefined\isGerman
    \input{#1de/#2}
    \else
    \ifdefined\isEnglish
    \input{#1en/#2}
    \else
    \input{#1de/#2}
    \fi
    \fi
}

\newcommand{\TRANS}[2]{
    \ifdefined\isGerman
    #1%
    \else
    \ifdefined\isEnglish
    #2%
    \else
    #1%
    \fi
    \fi
}

% muss für Akronyme \ac statt see verwendet werden.
\newcommand{\Siehe}{
    \ifdefined\isGerman
    \emph{siehe}
    \else
    \ifdefined\isEnglish
    \emph{see}
    \else
    \emph{siehe}
    \fi
    \fi
}

%todo Die Kommandos sind für das Endprodukt zu entfernen. Die entsprechenden Stellen sind zu bearbeiten bzw. zu löschen
\newcommand{\Mynote}[1]{\marginnote{\textcolor{red}{WS:#1}}}
\newcommand{\Ausblenden}[1]{}
\newcommand{\ToDo}[1]{\textcolor{red}{\section{ToDo} #1}}
% Fehlerzähler
\setul{0.5ex}{0.3ex}
\setulcolor{red}
\newcounter{fehlernummer}
\setcounter{fehlernummer}{11}
\newcommand{\FEHLER}[1]{\ul{#1}\stepcounter{fehlernummer}\textsuperscript{\textcolor{red}{\arabic{fehlernummer}}}}
%\renewcommand{\FEHLER}[1]{\ul{#1}\stepcounter{fehlernummer}\marginnote{\textcolor{red}{\arabic{fehlernummer}}}} geht leider nicht
%\renewcommand{\FEHLER}[1]{\ul{#1}\stepcounter{fehlernummer}\footnote{\textcolor{red}{\arabic{fehlernummer}.Fehler}}} geht leider nicht

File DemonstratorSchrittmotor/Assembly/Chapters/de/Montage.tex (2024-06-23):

%%%%%%%%%%%%
%
% $Autor: Theilmann $
% $Datum: 11.06.2024 $
% $Pfad: DemonstratorSchrittmotor\Assembly\Chapters\de\VorMontage.tex $
% $Version: 1 $
% !TeX spellcheck = en_GB/de_DE
% !TeX encoding = utf8
% !TeX root = MontageDemontageanleitung 
% !TeX TXS-program:bibliography = txs:///biber
%%%%%%%%%%%%

\chapter{Montage}\label{Mont}

In diesem Kapitel wird die Montage des Demonstrators für einen Schrittmotor Schritt für Schritt erläutert. Es wird empfohlen, die Schritte in der vorgegebenen Reihenfolge zu befolgen.

\section{Erster Schritt: Montieren Schaltnetzteil, Entwicklerboard und AMS1117}
 Montieren Sie die folgenden Bauteile und elektrischen Komponenten wie in Abbildung \ref{1.S} gezeigt. 
 
\begin{enumerate}
 	\item Befestigen Sie das Schaltnetzteil an der Bodenplatte mit 2 $\times$ $ M3 \times 10 \ mm $ Schrauben. Die Schrauben werden von der unteren Seite der Bodenplatte eingeführt. 
 	\item Nehmen Sie 2 $\times$ $ M3 \times 14 \ mm $ Schrauben und kontern Sie diese mit 2 $\times M3 $ Muttern gegen die Bodenplatte. Die Schrauben werden von der unteren Seite der Bodenplatte eingeführt.
 	\item Montieren Sie das Entwicklerboard Schrittmotorsteuerung A4988 auf der Bodenplatte. Verwenden Sie 2 $\times$ $ M3 \times 14 \ mm $ und 4 $\times$ $ M3 $ Muttern. Die Reihenfolge ist: Schraube - Bodenplatte - Mutter - Entwicklerboard - Mutter. Die Schrauben werden von der unteren Seite der Bodenplatte eingeführt.
 	\item Stecken Sie die Schrittmotorsteuerung in das Entwicklerboard und achten Sie auf die richtige Pinbelegung.
 	\item Setzen Sie den Spannungswandler AMS1117 in den Halter für AMS und setzen Sie den Clip auf. Befestigen Sie den Halter und den Clip mit einer  $\times$ $ M3 \times 14 \ mm $ Schraube
\end{enumerate}
 
\begin{figure}[H]
	\begin{center}
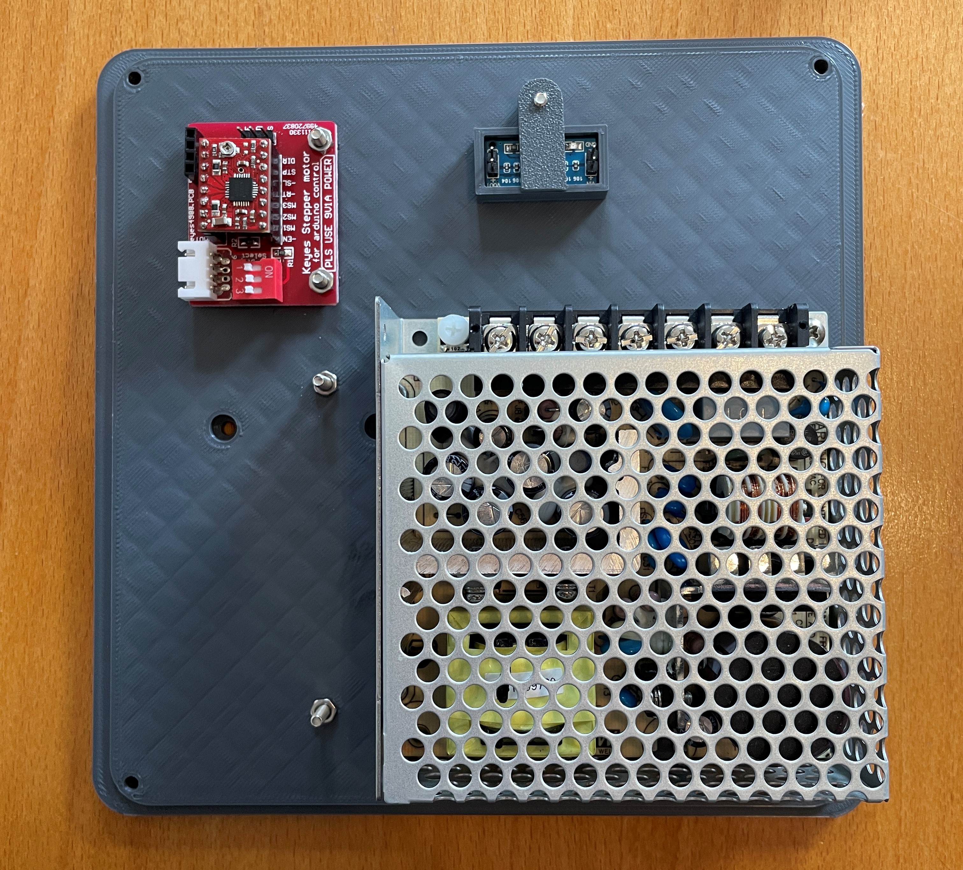
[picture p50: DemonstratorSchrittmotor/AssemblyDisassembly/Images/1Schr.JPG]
		
		\caption{Erster Schritt: Montieren Schaltnetzteil, Entwicklerboard und AMS1117} \label{1.S}
	\end{center}
\end{figure}

\section{Zweiter Schritt: Anbringen der Bodenplatte an Aluprofil}

Montieren Sie die folgenden Bauteile und elektrischen Komponenten wie in Abbildung \ref{2.S} gezeigt.

\begin{enumerate}
	\item Führen Sie 2 $\times$ $ M3 $ Hammermutter in das Aluprofil ein.
	\item Verschrauben Sie die Bodenplatte mit 2 $\times$ $ M3 \times 10 \ mm $ Schrauben an den Hammermuttern im Aluprofil, sodass die Bodenplatte bündig mit dem Profil abschließt.
	\item Setzen Sie das Tiny Machine Learning Shield (TMLS) auf die hervorstehenden Schrauben und sichern Sie es mit 2 $\times$ $ M3 $ Muttern.
	Stecken Sie den Arduino Nano Sense BLE 33 Lite auf das TMLS und achten Sie dabei auf die Pinbelegung.
\end{enumerate}

\begin{figure}[H]
	\begin{center}
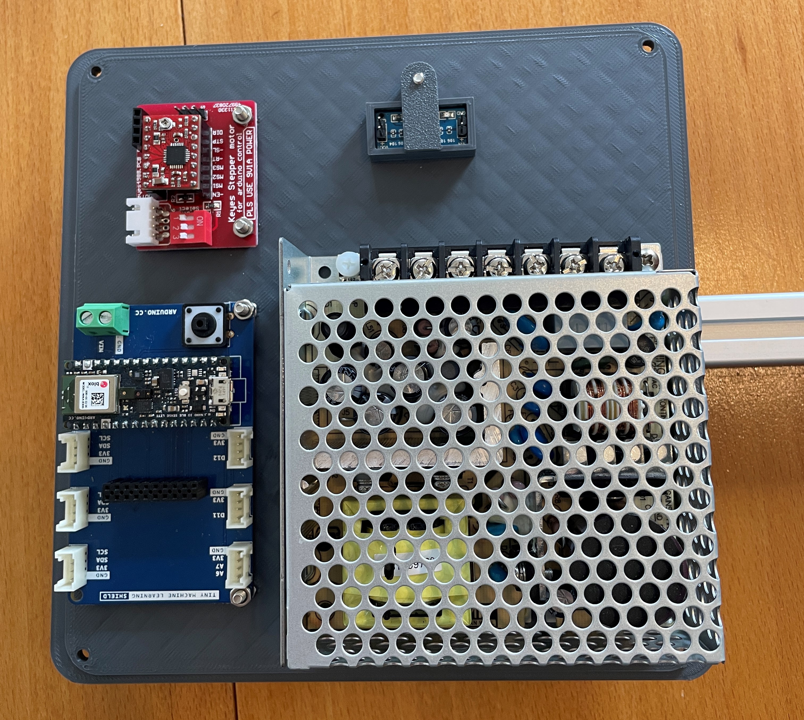
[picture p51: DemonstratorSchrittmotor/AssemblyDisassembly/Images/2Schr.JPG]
		
		\caption{Zweiter Schritt: Anbringen der Bodenplatte an Aluprofil} \label{2.S}
	\end{center}
\end{figure}

\section{Dritter Schritt: Zusammenbau der Vorderplatte}

Montieren Sie die folgenden Bauteile und elektrischen Komponenten wie in Abbildung \ref{3.S} gezeigt.

\begin{enumerate}
	\item Befestigen Sie das OLED-Display mit 2 $\times$ $ M3 \times 6 \ mm $ Schrauben in die dafür vorgesehenen \O 2,8 \ mm Bohrungen der Vorderplatte.
	\item Führen Sie die SMD-LED in die \O 8 \ mm Bohrung der Vorderen Platte ein.
	\item Führen Sie den Drehwinkel-Encoder in die \O 7 \ mm Bohrung ein und kontern Sie diese mit der P-4 Mutter.
	\item Führen Sie den Druckknopf in die \O 13,5 \ mm Bohrung und kontern Sie den mit der zugehörigen Mutter.
\end{enumerate}

\begin{figure}[H]
	\begin{center}
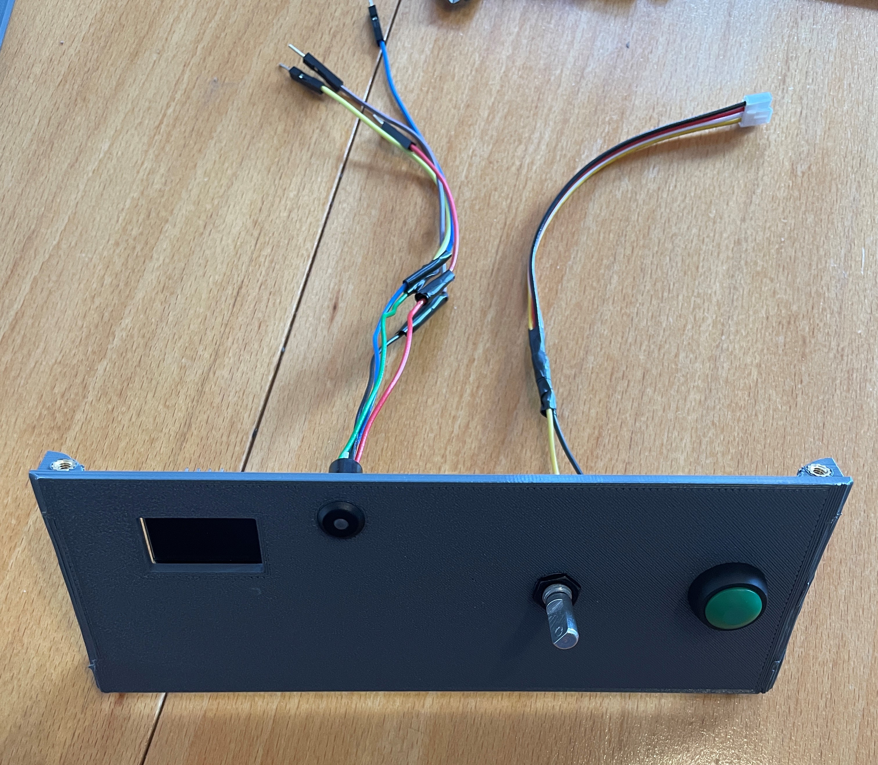
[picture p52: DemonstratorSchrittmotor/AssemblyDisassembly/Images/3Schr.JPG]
		
		\caption{Dritter Schritt: Zusammenbau der Vorderplatte} \label{3.S}
	\end{center}
\end{figure}

\section{Vierter Schritt: Zusammenbau der Hinterplatte}

Montieren Sie die folgenden Bauteile und elektrischen Komponenten wie in Abbildung \ref{4.S} gezeigt. 

\begin{enumerate}
	\item Montieren Sie den Kaltgeräteanschluss an der Hinterplatte. Ein Klickgeräusch bestätigt den korrekten Sitz.
\end{enumerate}

\begin{figure}[H]
	\begin{center}
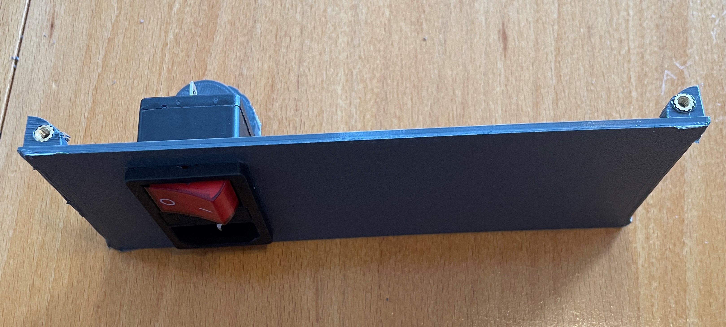
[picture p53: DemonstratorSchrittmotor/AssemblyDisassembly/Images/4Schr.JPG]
		
		\caption{Vierter Schritt: Zusammenbau der Hinterplatte} \label{4.S}
	\end{center}
\end{figure}

\section{Fünfter Schritt: Teilzusammenbau des Gehäuses}

Montieren Sie die folgenden Bauteile und elektrischen Komponenten wie in Abbildung \ref{5.S} gezeigt. 

\begin{enumerate}
	\item Verschrauben Sie die Vorderplatte und die Hinterplatte mit der Bodenplatte. Verwenden Sie dafür 4 $\times$ $ M3 \times 10 \ mm $ Schrauben.
	\item Befestigen Sie die rechte Seitenplatte mit der Vorder- und Hinterplatte. Verwenden Sie dafür 2 $\times$ $ M3 \times 10 \ mm $ Schrauben.
\end{enumerate}

\begin{figure}[H]
	\begin{center}
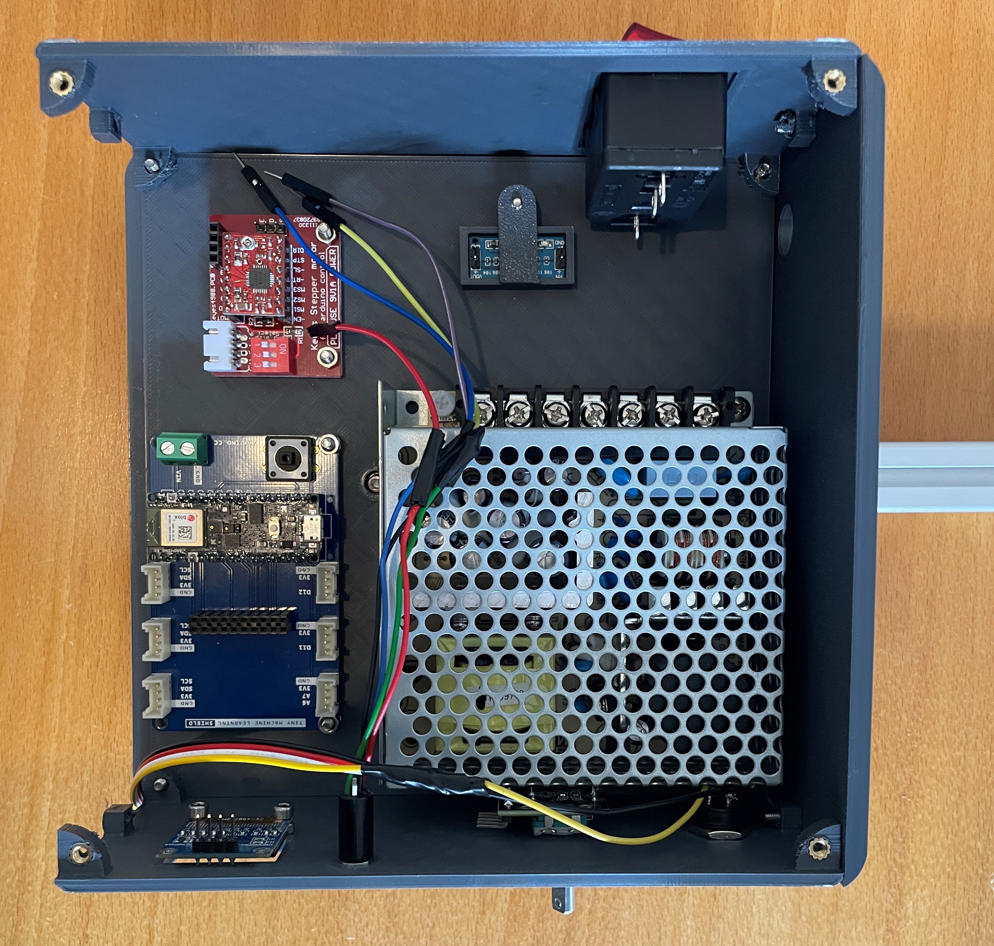
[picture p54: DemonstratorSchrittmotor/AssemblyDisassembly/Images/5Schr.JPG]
		
		\caption{Fünfter Schritt: Teilzusammenbau des Gehäuses} \label{5.S}
	\end{center}
\end{figure}

\section{Sechster Schritt: Anschließen der elektrischen Leitungen}

\begin{enumerate}
	\item Verbinden Sie die Leitungen gemäß dem Schaltplan (siehe Abbildung \ref{Splan}). Dieser Schritt sollte von einer Elektrofachkraft durchgeführt oder überprüft werden.
	\item Führen Sie die Leitungen für den Motor und den Micro-Schalter durch die Öffnung in der rechten Seitenplatte.
\end{enumerate}

\begin{figure}[H]
	\begin{center}
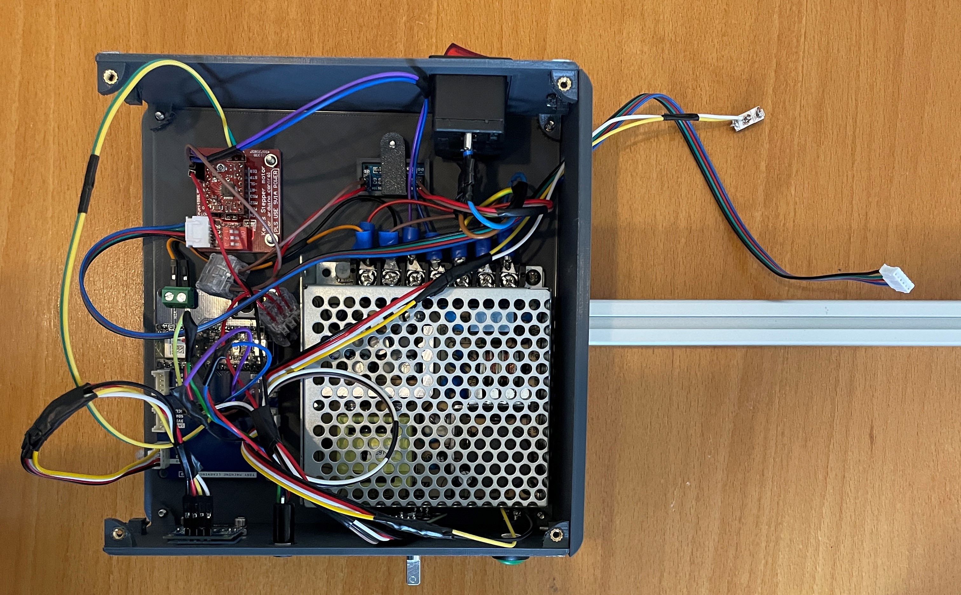
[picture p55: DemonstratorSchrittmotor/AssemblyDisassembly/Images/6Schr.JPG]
		
		\caption{Schaltplan} \label{6.S}
	\end{center}
\end{figure}

\section{Siebter Schritt: Montieren des Micro-Schalters und Motors}

Montieren Sie die folgenden Bauteile und elektrischen Komponenten wie in Abbildung \ref{7.S} gezeigt.

\begin{enumerate}
	\item Befestigen Sie den Micro-Schalter mit 2 $\times$ $ M2.5 \times 6 \ mm $ Schrauben an der Halterung für den Motor.
	\item Montieren Sie den Nema 17 Motor an der Halterung für die Welle mit 4 $\times$ $ M3 \times 6 \ mm  $ Schrauben.
	\item Führen Sie 2 $\times$ $ M3 $ Hammermutter in das Aluprofil ein.
	\item Befestigen Sie die Halterung am Aluprofil mit 2 $\times$ $ M3 \times 8 \ mm $ und 2 $\times$ $ M3 $ Hammermuttern. Halten Sie einen Abstand vom Gehäuse von ca. 15 bis 20 \ mm. 
	\item Verbinden Sie die Leitung für den Motor an dem Motor. 
\end{enumerate}

\begin{figure}[H]
	\begin{center}
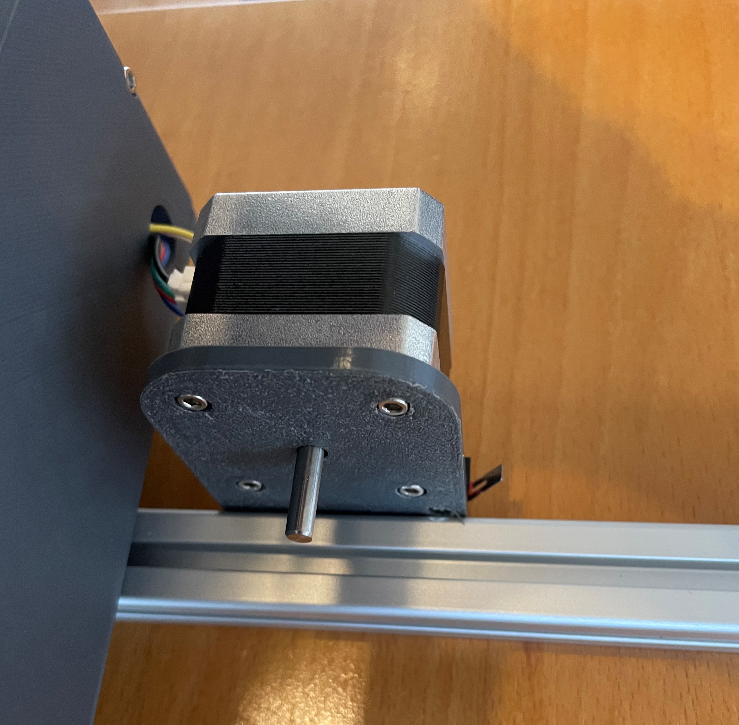
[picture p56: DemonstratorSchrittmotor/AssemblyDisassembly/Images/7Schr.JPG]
		
		\caption{Siebter Schritt: Montieren des Micro-Schalters und Motors} \label{7.S}
	\end{center}
\end{figure}

\section{Achter Schritt: Zusammenbau des Gehäuses}

Montieren Sie die folgenden Bauteile und elektrischen Komponenten wie in Abbildung \ref{8.S} gezeigt.

\begin{enumerate}
	\item Verschrauben Sie die Seitenplatte Links und die Hinterplatte mit der Vorderplatte und Hinterplatte. Verwenden Sie dafür 2 $\times$ $ M3 \times 10 \ mm $ Schrauben.
	\item Verschrauben Sie die Deckelplatte mit der Vorderplatte und Hinterplatte. Verwenden Sie dafür 4 $\times$ $ M3 \times 10 \ mm $ Schrauben.
\end{enumerate}

\begin{figure}[H]
	\begin{center}
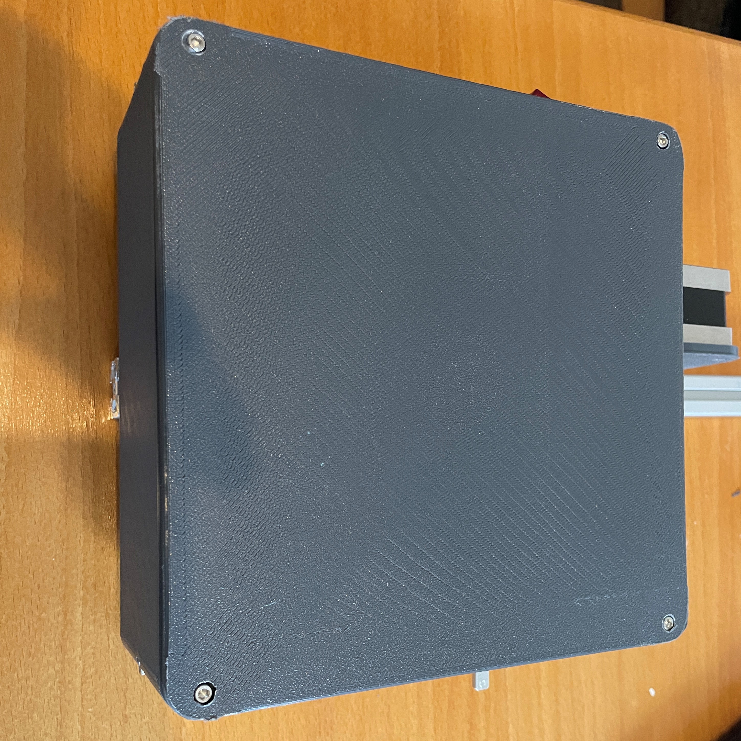
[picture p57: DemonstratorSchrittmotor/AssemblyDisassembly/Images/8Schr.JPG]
		
		\caption{Achter Schritt: Zusammenbau des Gehäuses} \label{8.S}
	\end{center}
\end{figure}

\section{Neunter Schritt: Montieren der Linearführung}

Montieren Sie die folgenden Bauteile wie in Abbildung \ref{9.S} gezeigt.

\begin{enumerate}
	\item Führen Sie 5 $\times$ $ M3 $ Hammermutter in das Aluprofil ein.
	\item Befestigen Sie die Liniearführung am Aluprofil mit 5 $\times$ $ M3 \times 10 \ mm $ und 5 $\times$ $ M3 $ Hammermuttern. Lassen Sie an jeder Seite eine Bohrung frei und nutzen Sie dann jede fünfte Bohrung. 
\end{enumerate}

\begin{figure}[H]
	\begin{center}
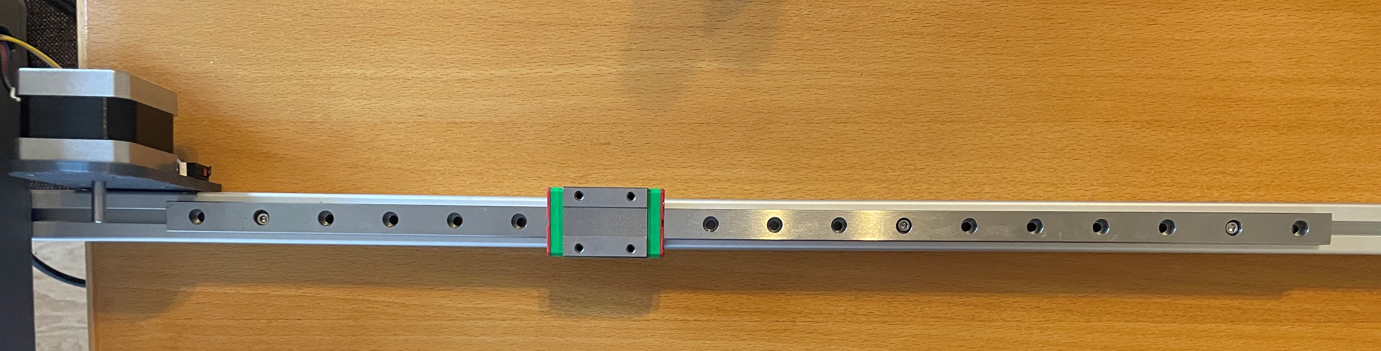
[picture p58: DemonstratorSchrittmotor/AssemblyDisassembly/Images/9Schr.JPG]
		
		\caption{Neunter Schritt: Montage der Liniearführung} \label{9.S}
	\end{center}
\end{figure}

\section{Zehnter Schritt: Montieren des Griffs}
Montieren Sie die folgenden Bauteile wie in Abbildung \ref{10.S} gezeigt.

\begin{enumerate}
	\item Führen Sie 2 $\times$ $ M3 $ Hammermutter in das Aluprofil ein.
	\item Montieren Sie den Anzeiger auf den Schlitten der Liniearführung mit 4 $\times$ $ M3 \times 6 \ mm $ Schrauben.
	\item Montieren Sie den Riemen Auf den Anzeiger mit 4 $\times$ $ M3 \times 6 \ mm $ Schrauben.
\end{enumerate}

\begin{figure}[H]
	\begin{center}
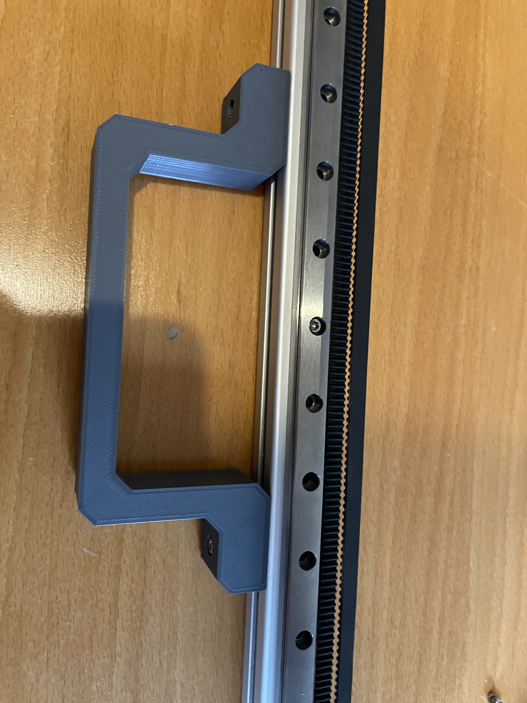
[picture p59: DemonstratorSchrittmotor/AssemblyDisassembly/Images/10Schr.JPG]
		
		\caption{Dreizehnter Schritt:Montieren des Griffs} \label{10.S}
	\end{center}
\end{figure}

\section{Elfter Schritt: Montieren der Halter für die Welle}

Montieren Sie die folgenden Bauteile wie in Abbildung \ref{11.S} gezeigt.

\begin{enumerate}
	\item Führen Sie jeweils 2 $\times$ $ M3 $ Hammermutter gegenüberliegend in das Aluprofil ein. Führen Sie außerdem 2 $\times$ $ M3 $ Hammermutter an der vorderen Seite für die spätere Montage des Lineals ein. 
	\item Befestigen Sie die erste Halterung am Aluprofil mit 2 $\times$ $ M3 \times 8 \ mm $ und 2 $\times$ $ M3 $ Hammermuttern.
	\item Führen Sie die Welle in die \O 7 \ mm Bohrung der Halterung ein.
	\item Stecken Sie auf die Welle die Riemenscheibe.
	\item Befestigen Sie die zweite Halterung gegenüberliegend der ersten Halterung am Aluprofil mit 2 $\times$ $ M3 \times 8 \ mm $ und 2 $\times$ $ M3 $ Hammermuttern.
\end{enumerate}

\begin{figure}[H]
	\begin{center}
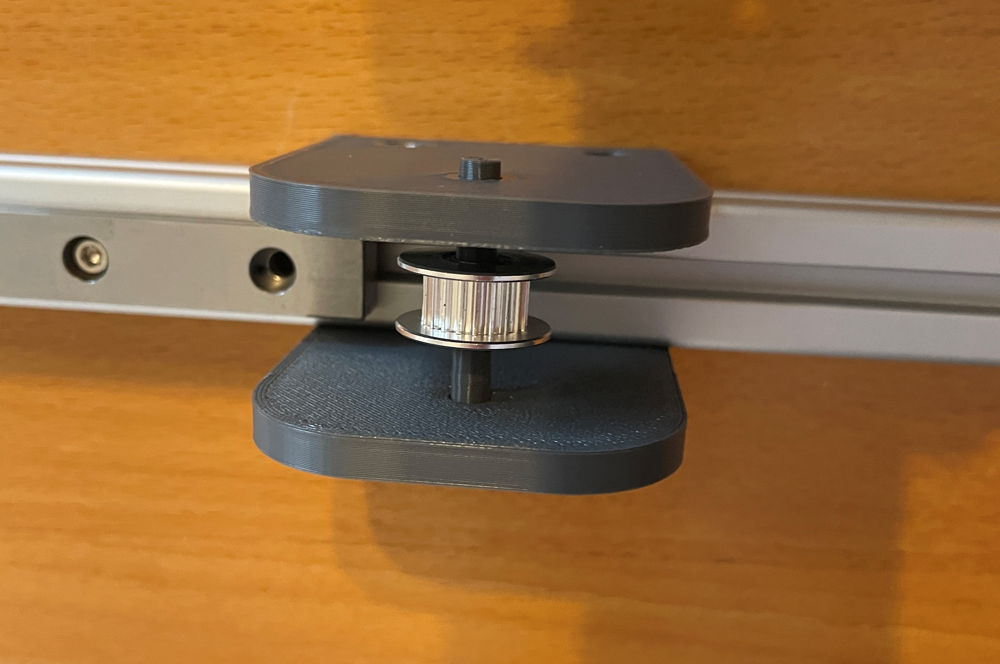
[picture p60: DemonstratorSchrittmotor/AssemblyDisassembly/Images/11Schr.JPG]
		
		\caption{Elfter Schritt: Montieren der Halter für die Welle} \label{11.S}
	\end{center}
\end{figure}

\section{Zwölfter Schritt: Montieren der Riemenscheibe am Motor}

Montieren Sie die folgenden Bauteile wie in Abbildung \ref{11.S} gezeigt.

\begin{enumerate}
	\item Montieren Sie die Riemenscheibe auf die Welle des Nema 17 Motors und befestigen Sie den mit den Madenschrauben in der Riemenscheibe. 
\end{enumerate}

\begin{figure}[H]
	\begin{center}
		
		\caption{Zwölfter Schritt: Montieren der Riemenscheibe am Motor} \label{12.S}
	\end{center}
\end{figure}

\section{Dreizehnter Schritt: Montieren des Anzeigers und des Riemens}

Montieren Sie die folgenden Bauteile wie in Abbildung \ref{13.S} gezeigt.

\begin{enumerate}
	\item Montieren Sie den Anzeiger auf den Schlitten der Liniearführung mit 4 $\times$ $ M3 \times 6 \ mm $ Schrauben.
	\item Montieren Sie den Riemen Auf den Anzeiger mit 4 $\times$ $ M3 \times 6 \ mm $ Schrauben.
\end{enumerate}

\begin{figure}[H]
	\begin{center}
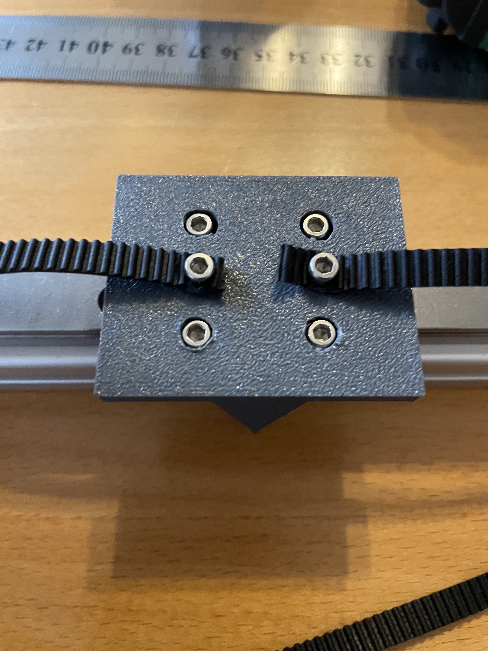
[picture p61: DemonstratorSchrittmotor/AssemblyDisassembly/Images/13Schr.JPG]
		
		\caption{Zwölfter Schritt: Montieren des Anzeigers und des Riemens} \label{13.S}
	\end{center}
\end{figure}

\section{Vierzehnter Schritt: Montieren des Lineals}

\begin{enumerate}
	\item Montieren Sie das Lineal auf den Schlitten der Liniearführung mit 4 $\times$ $ M3 \times 6 \ mm $ Schrauben mit dem im Schritt 11 eingesetzten 2 $\times$ $ M3 $ Hammermutter.
\end{enumerate}

\section{Abschlussarbeiten}

\begin{enumerate}
	\item Überprüfen Sie alle Verbindungen und Schrauben auf festen Sitz.
	\item Testen Sie Mithilfe des Manuals die Funktionsfähigkeit des Demonstrators. 
\end{enumerate}

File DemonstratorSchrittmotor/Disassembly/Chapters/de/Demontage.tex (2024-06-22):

%%%%%%%%%%%%
%
% $Autor: Theilmann $
% $Datum: 12.06.2024 $
% $Pfad:DemonstratorSchrittmotor\Disassembly\Chapters\de\Demontage.tex $
% $Version: 1 $
% !TeX spellcheck = en_GB/de_DE
% !TeX encoding = utf8
% !TeX root = MontageDemontageanleitung 
% !TeX TXS-program:bibliography = txs:///biber
%%%%%%%%%%%%

\chapter{Demontage}
In diesem Kapitel wird die Montage des Demonstrators für einen Schrittmotor erläutert. Es wird empfohlen, die Schritte in der vorgegebenen Reihenfolge zu befolgen.

\section{ Vorbereitung zur Demontage}

\textbf{Sicherheitsüberprüfung:}\begin{itemize}
		\item Trennen Sie den Demonstrator vom Stromnetz 
		\item Entfernen Sie das Netzkabel aus dem Kaltgeräteanschluss
	\end{itemize}

\section{ Demontage in umgekehrte Reihenfolger der Montage}

Demontieren Sie den Demonstrator in umgekehrter Reihenfolge zur Montage (siehe Montageanleitung).

\section{ Demontage der Einpressmutter}

Erhitzen Sie die Einpressmuttern mit dem Lötkolben, bis sich die Mutter augenscheinlich bewegt. Nachfolgend schrauben Sie eine ausreichend lange M3 Schraube hinein und ziehen an der Schraube.

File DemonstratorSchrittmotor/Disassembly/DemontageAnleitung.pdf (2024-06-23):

## Demontageanleitung

## Demonstrator für einen Schrittmotor

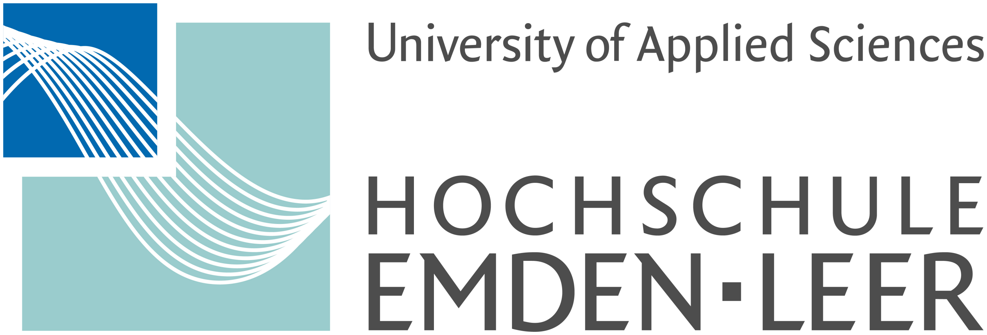
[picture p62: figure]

Autor: | Maik Theilmann
Matrikel-Nr.: | 7021861
Autor: | Jannik Grönke
Matrikel-Nr.: | 7022006
Autor: | Enno Stein
Matrikel-Nr.: | 7021960
Autor: | Lars Hanneken
Matrikel-Nr.: | 7021910
Autor: | Jan ter Veen
Matrikel-Nr.: | 7022071
Studiengang: | Maschinenbau
Erstprüfer: | Prof. Dr. Elmar Wings
Abgabedatum: | 23. Juni 2024

Hochschule Emden/Leer · Fachbereich Technik · Abteilung Maschinenbau Constantiaplatz 4 · 26723 Emden · http://www.hs-emden-leer.de

2

## Inhaltsverzeichnis

Abbildungsverzeichnis | iii
Tabellenverzeichnis | v
Abkürzungen | vii
1 Demontage | 1

i

## Abbildungsverzeichnis

iii

## Tabellenverzeichnis

v

## Abkürzungen

vii

## 1 Demontage

In diesem Kapitel wird die Montage des Demonstrators für einen Schrittmotor erläutert. Es wird empfohlen, die Schritte in der vorgegebenen Reihenfolge zu befolgen.

1.1 Vorbereitung zur Demontage

Sicherheitsüberprüfung:
- Trennen Sie den Demonstrator vom Stromnetz
- Entfernen Sie das Netzkabel aus dem Kaltgeräteanschluss

1.2 Demontage in umgekehrte Reihenfolger der Montage

Demontieren Sie den Demonstrator in umgekehrter Reihenfolge zur Montage (siehe Montageanleitung).

1.3 Demontage der Einpressmutter

Erhitzen Sie die Einpressmuttern mit dem Lötkolben, bis sich die Mutter augenscheinlich bewegt. Nachfolgend schrauben Sie eine ausreichend lange M3 Schraube hinein und ziehen an der Schraube.

1

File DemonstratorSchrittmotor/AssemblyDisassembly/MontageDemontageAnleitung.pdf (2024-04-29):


## Montage- & Demontageanleitung

## Demonstrator für einen Schrittmotor

Autor: | Maik Theilmann
Matrikel-Nr.: | 7021861
Autor: | Jannik Grönke
Matrikel-Nr.: | 7022006
Autor: | Enno Stein
Matrikel-Nr.: | 7021960
Autor: | Lars Hanneken
Matrikel-Nr.: | 7021910
Autor: | Jan ter Veen
Matrikel-Nr.: | 7022071
Studiengang: | Maschinenbau
Erstprüfer: | Prof. Dr. Elmar Wings
Abgabedatum: | 29. April 2024

Hochschule Emden/Leer · Fachbereich Technik · Abteilung Maschinenbau Constantiaplatz 4 · 26723 Emden · http://www.hs-emden-leer.de

2

# Inhaltsverzeichnis

Abbildungsverzeichnis | iii
Tabellenverzeichnis | v
Abkürzungen | vii

i

# Abbildungsverzeichnis

iii

# Tabellenverzeichnis

v

# Abkürzungen

vii

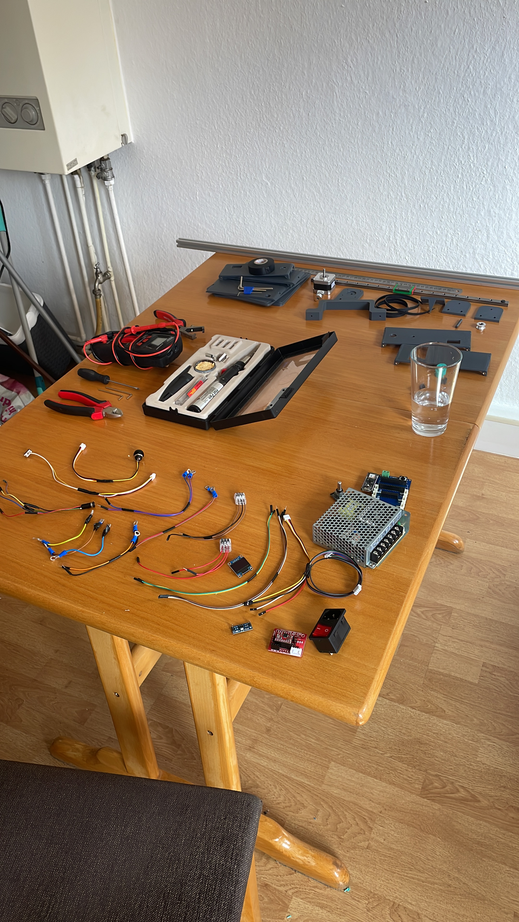
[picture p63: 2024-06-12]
DemonstratorSchrittmotor/Disassembly/Images/C71F794E-9673-4758-A72E-BA9C8B1C6161.JPG

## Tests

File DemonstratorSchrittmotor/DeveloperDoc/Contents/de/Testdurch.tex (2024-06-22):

%%%%%%%%%%%%%%%%%%%%
%
% $Beschreibung: Erklärung und Durchführung der Tests $
% $Autor: Theilmann und Hanneken $
% $Datum: 15.05.2024 $
% $Pfad: DemonstratorSchrittmotor/DeveloperDoc/Contents/de/Testdurch.tex $
% $Version: 3 $
%
%
%%%%%%%%%%%%%%%%%%%
\chapter{Testdurchläufe}

Ein fehlerfreier Ablauf kann nie vollständig gewährleistet werden, es können stets zufällige Fehler auftreten. Um die Funktionalität und Zuverlässigkeit des Systems zu gewährleisten, sind regelmäßige Testdurchläufe notwendig. Eine erste Überprüfung findet mit der Sichtprüfung der Hardware auf Schäden statt. Für die softwareseitige Überprüfung können Testprogramme nach Einschalten durchlaufen werden.  

\section{Arduino Nano 33 BLE Sense Lite}

Für die Überprüfung des Arduinos, werden Beispielsketche von der Arduino IDE zur Verfügung gestellt. Unter dem Pfad File/Examples/01.Basics können Beispielsketche ausgesucht werden. Mit dem Beispielprogramm Blink wird die Built In LED angesprochen. Bei richtiger Funktion des Arduinos sollte die LED für eine Sekunde eingeschaltet und für eine Sekunde ausgeschaltet werden. Dieses wiederholt sich fortlaufend. Dadurch ist die Ansteuerung des Arduinos sichergestellt.
Der Code dieser Anwendung wird detaillierter im Kapitel \ref{ersterprogrammtest} erläutert.

\section{Schaltnetzteil}

Die Überprüfung des Schaltnetzteils \textbf{muss} von einer Elektrofachkraft durchgeführt werden. Ist das Schaltnetzteil ordnungsgemäß angeschlossen, leuchtet eine Signalleuchte Grün auf dem Schaltnetzteil. Um eine einwandfreie Nutzung zu gewährleisten müssen noch die Ausgangsspannungen des Netzteils mit einem Voltmeter überprüft werden. Liegen die Ausgangsspannungen jeweils bei 12 \ V und 5 V \ ist eine einwandfreie Nutzung gewährleistet. 

\section{Spannungsregler AMS1117}

Ist der Spannungswandler ordnungsgemäß angeschlossen, leuchtet eine Signalleuchte Rot auf dem AMS1177. Um eine einwandfreie Nutzung zu gewährleisten muss noch die Ausgangsspannung des Spannungswandlers mit einem Voltmeter überprüft werden. Liegt die Ausgangsspannungen bei 3,3 \ V ist eine einwandfreie Nutzung gewährleistet. 

\section{ Nema 17 Schrittmotor mit Schrittmotorsteuerung A4988 }

Die korrekte Verbindung der Pins sowie der Schrittmotorsteuerung wird durch das folgende Testprogramm \ref{Code:Testprogramm für den Schrittmotor} getestet. Hierbei wird der Schrittmotor in einer fest gelegten Geschwindigkeit rotiert. \cite{MikeMcCauley.2024}:

\begin{code}[H]
	\begin{lstlisting}[language=c++]
	#include "AccelStepper.h"
	
	#define dirPin 0
	#define stepPin 8
	#define motorInterfaceType 1
	
	AccelStepper stepper = AccelStepper(motorInterfaceType, stepPin, dirPin);
	
	void setup() {
		stepper.setMaxSpeed(1000);
		stepper.setAcceleration(1000);
	}
	
	void loop() {
		stepper.setSpeed(500);
		stepper.runSpeed();
	}
\end{lstlisting}      

\caption[Testprogramm für den Schrittmotor]{Testprogramm für den Schrittmotor}\label{Code:Testprogramm für den Schrittmotor}    
\end{code} 

Zunächst hat die Ansteuerung des Motors nicht wie geplant funktioniert, statt zu rotieren, vibrierte der Motor lediglich. Nach der Überprüfung der Innenwiderstände am Motor und dem Abgleich mit dem Anschlussplan der Schrittmotorsteuerung wurde deutlich, dass die Zuordnung der Pins am Steckkabel nicht korrekt waren. Durch die Umpolung des Steckkabels konnte die korrekte Ansteuerung des Schrittmotors hergestellt und bestätigt werden.

\section{OLED-Display}

Um die Funktion und korrekte Ansteuerung des OLED-Displays zu testen, wird ein Testprogramm (Listing \ref{Code:Testprogramm für das OLED-Display}) verwendet, welches nacheinander verschiedene Abbildungen und Animationen auf dem Display darstellt und abspielt \cite{RuiSantos.2016}:

\begin{code} [H]
	\begin{lstlisting}[language=c++]
	#include <SPI.h>
	#include <Wire.h>
	#include <Adafruit_GFX.h>
	#include <Adafruit_SSD1306.h>
	
	#define SCREEN_WIDTH 128
	#define SCREEN_HEIGHT 64
	
	#define OLED_RESET -1
	#define SCREEN_ADDRESS 0x3C
	Adafruit_SSD1306 display(SCREEN_WIDTH, SCREEN_HEIGHT, &Wire, OLED_RESET);
	
	#define NUMFLAKES 10
	
	#define LOGO_HEIGHT 16
	#define LOGO_WIDTH 16
	static const unsigned char PROGMEM logo_bmp[] =
	{ 0b00000000, 0b11000000,
		0b00000001, 0b11000000,
		0b00000001, 0b11000000,
		0b00000011, 0b11100000,
		0b11110011, 0b11100000,
		0b11111110, 0b11111000,
		0b01111110, 0b11111111,
		0b00110011, 0b10011111,
		0b00011111, 0b11111100,
		0b00001101, 0b01110000,
		0b00011011, 0b10100000,
		0b00111111, 0b11100000,
		0b00111111, 0b11110000,
		0b01111100, 0b11110000,
		0b01110000, 0b01110000,
		0b00000000, 0b00110000 };
	
	void setup() {
		Serial.begin(9600);
		
		if(!display.begin(SSD1306_SWITCHCAPVCC, SCREEN_ADDRESS)) {
			Serial.println(F("SSD1306 allocation failed"));
			for(;;);
		}
		
		display.display();
		delay(2000);
		
		display.clearDisplay();
		
		display.drawPixel(10, 10, SSD1306_WHITE);
		display.display();
		delay(2000);
		
\end{lstlisting} 
\end{code}

\begin{code} [H]	
\begin{lstlisting} 

		testdrawline();
		testdrawrect();
		testfillrect();
		testdrawcircle();
		testfillcircle();
		testdrawroundrect();
		testfillroundrect();
		testdrawtriangle();
		testfilltriangle();
		testdrawchar();
		testdrawstyles();
		testscrolltext();
		testdrawbitmap();
		
		display.invertDisplay(true);
		delay(1000);
		display.invertDisplay(false);
		delay(1000);
		
		testanimate(logo_bmp, LOGO_WIDTH, LOGO_HEIGHT);
	}
	
	void loop() {
	}
	
	void testdrawline() {
		int16_t i;
		
		display.clearDisplay();
		
		for(i=0; i<display.width(); i+=4) {
			display.drawLine(0, 0, i, display.height()-1, SSD1306_WHITE);
			display.display();
			delay(1);
		}
		for(i=0; i<display.height(); i+=4) {
			display.drawLine(0, 0, display.width()-1, i, SSD1306_WHITE);
			display.display();
			delay(1);
		}
		delay(250);
		
		display.clearDisplay();
		
		for(i=0; i<display.width(); i+=4) {
			display.drawLine(0, display.height()-1, i, 0, SSD1306_WHITE);
			display.display();
			delay(1);
		}
		
\end{lstlisting} 
\end{code}

\begin{code} [H]	
\begin{lstlisting} 
	
		for(i=display.height()-1; i>=0; i-=4) {
			display.drawLine(0, display.height()-1, display.width()-1, i, SSD1306_WHITE);
			display.display();
			delay(1);
		}
		delay(250);
				
		display.clearDisplay();
		
		for(i=display.width()-1; i>=0; i-=4) {
			display.drawLine(display.width()-1, display.height()-1, i, 0, SSD1306_WHITE);
			display.display();
			delay(1);
		}
		for(i=display.height()-1; i>=0; i-=4) {
			display.drawLine(display.width()-1, display.height()-1, 0, i, SSD1306_WHITE);
			display.display();
			delay(1);
		}
		delay(250);
		
		display.clearDisplay();
				
		for(i=0; i<display.height(); i+=4) {
			display.drawLine(display.width()-1, 0, 0, i, SSD1306_WHITE);
			display.display();
			delay(1);
		}
		for(i=0; i<display.width(); i+=4) {
			display.drawLine(display.width()-1, 0, i, display.height()-1, SSD1306_WHITE);
			display.display();
			delay(1);
		}
		
		delay(2000);
	}

\end{lstlisting} 
\end{code}

\begin{code} [H]	
\begin{lstlisting} 

	void testdrawrect() {
		display.clearDisplay();
		
		for(int16_t i=0; i<display.height()/2; i+=2) {
			display.drawRect(i, i, display.width()-2*i, display.height()-2*i, SSD1306_WHITE);
			display.display();
			delay(1);
		}
		
		delay(2000);
	}
	
	void testfillrect() {
		display.clearDisplay();
		
		for(int16_t i=0; i<display.height()/2; i+=3) {
			display.fillRect(i, i, display.width()-i*2, display.height()-i*2, SSD1306_INVERSE);
			display.display();
			delay(1);
		}
		
		delay(2000);
	}
	
	void testdrawcircle() {
		display.clearDisplay();
		
		for(int16_t i=0; i<max(display.width(),display.height())/2; i+=2) {
			display.drawCircle(display.width()/2, display.height()/2, i, SSD1306_WHITE);
			display.display();
			delay(1);
		}
		
		delay(2000);
	}
	
	void testfillcircle() {
		display.clearDisplay();
		
		for(int16_t i=max(display.width(),display.height())/2; i>0; i-=3) {
			display.fillCircle(display.width() / 2, display.height() / 2, i, SSD1306_INVERSE);
			display.display();
			delay(1);
		}
		
		delay(2000);
	}

\end{lstlisting} 
\end{code}

\begin{code} [H]	
\begin{lstlisting} 
	
	void testdrawroundrect() {
		display.clearDisplay();
		
		for(int16_t i=0; i<display.height()/2-2; i+=2) {
			display.drawRoundRect(i, i, display.width()-2*i, display.height()-2*i,
			display.height()/4, SSD1306_WHITE);
			display.display();
			delay(1);
		}
		
		delay(2000);
	}
	
	void testfillroundrect() {
		display.clearDisplay();
		
		for(int16_t i=0; i<display.height()/2-2; i+=2) {
			display.fillRoundRect(i, i, display.width()-2*i, display.height()-2*i,
			display.height()/4, SSD1306_INVERSE);
			display.display();
			delay(1);
		}
		
		delay(2000);
	}
	
	void testdrawtriangle() {
		display.clearDisplay();
		
		for(int16_t i=0; i<max(display.width(),display.height())/2; i+=5) {
			display.drawTriangle(
			display.width()/2  , display.height()/2-i,
			display.width()/2-i, display.height()/2+i,
			display.width()/2+i, display.height()/2+i, SSD1306_WHITE);
			display.display();
			delay(1);
		}
		
		delay(2000);
	}
	
	void testfilltriangle() {
		display.clearDisplay();
		
\end{lstlisting} 
\end{code}

\begin{code} [H]	
\begin{lstlisting} 
		
		for(int16_t i=max(display.width(),display.height())/2; i>0; i-=5) {
			display.fillTriangle(
			display.width()/2  , display.height()/2-i,
			display.width()/2-i, display.height()/2+i,
			display.width()/2+i, display.height()/2+i, SSD1306_INVERSE);
			display.display();
			delay(1);
		}
		
		delay(2000);
	}
	
	void testdrawchar() {
		display.clearDisplay();
		
		display.setTextSize(1);
		display.setTextColor(SSD1306_WHITE);
		display.setCursor(0, 0);
		display.cp437(true);
		
		for(int16_t i=0; i<256; i++) {
			if(i == '\n') display.write(' ');
			else          display.write(i);
		}
		
		display.display();
		delay(2000);
	}
	
	void testdrawstyles() {
		display.clearDisplay();
		
		display.setTextSize(1);
		display.setTextColor(SSD1306_WHITE);
		display.setCursor(0,0);
		display.println(F("Hello, world!"));
		
		display.setTextColor(SSD1306_BLACK, SSD1306_WHITE);
		display.println(3.141592);
		
		display.setTextSize(2);
		display.setTextColor(SSD1306_WHITE);
		display.print(F("0x")); display.println(0xDEADBEEF, HEX);
		
		display.display();
		delay(2000);
	}
	
	\end{lstlisting} 
\end{code}

\begin{code} [H]	
\begin{lstlisting} 
	
	void testscrolltext() {
		display.clearDisplay();
		
		display.setTextSize(2);
		display.setTextColor(SSD1306_WHITE);
		display.setCursor(10, 0);
		display.println(F("scroll"));
		display.display();
		delay(100);
		
		display.startscrollright(0x00, 0x0F);
		delay(2000);
		display.stopscroll();
		delay(1000);
		display.startscrollleft(0x00, 0x0F);
		delay(2000);
		display.stopscroll();
		delay(1000);
		display.startscrolldiagright(0x00, 0x07);
		delay(2000);
		display.startscrolldiagleft(0x00, 0x07);
		delay(2000);
		display.stopscroll();
		delay(1000);
	}
	
	void testdrawbitmap() {
		display.clearDisplay();
		
		display.drawBitmap(
		(display.width()  - LOGO_WIDTH ) / 2,
		(display.height() - LOGO_HEIGHT) / 2,
		logo_bmp, LOGO_WIDTH, LOGO_HEIGHT, 1);
		display.display();
		delay(1000);
	}
	
	#define XPOS 0
	#define YPOS 1
	#define DELTAY 2
	
	void testanimate(const uint8_t *bitmap, uint8_t w, uint8_t h) {
		int8_t f, icons[NUMFLAKES][3];

\end{lstlisting} 
\end{code}

\begin{code} [H]	
\begin{lstlisting} 
		
		for(f=0; f< NUMFLAKES; f++) {
			icons[f][XPOS]   = random(1 - LOGO_WIDTH, display.width());
			icons[f][YPOS]   = -LOGO_HEIGHT;
			icons[f][DELTAY] = random(1, 6);
			Serial.print(F("x: "));
			Serial.print(icons[f][XPOS], DEC);
			Serial.print(F(" y: "));
			Serial.print(icons[f][YPOS], DEC);
			Serial.print(F(" dy: "));
			Serial.println(icons[f][DELTAY], DEC);
		}
		
		for(;;) {
			display.clearDisplay();
			
			for(f=0; f< NUMFLAKES; f++) {
				display.drawBitmap(icons[f][XPOS], icons[f][YPOS], bitmap, w, h, SSD1306_WHITE);
			}
			
			display.display();
			delay(200);
			
			for(f=0; f< NUMFLAKES; f++) {
				icons[f][YPOS] += icons[f][DELTAY];
				if (icons[f][YPOS] >= display.height()) {
					icons[f][XPOS]   = random(1 - LOGO_WIDTH, display.width());
					icons[f][YPOS]   = -LOGO_HEIGHT;
					icons[f][DELTAY] = random(1, 6);
				}
			}
		}
	}
\end{lstlisting}      

\caption[Testprogramm für das OLED-Display]{Testprogramm für das OLED-Display}\label{Code:Testprogramm für das OLED-Display}    
\end{code} 

Mit Hilfe dieses Beispielprogrammes \ref{Code:Testprogramm für das OLED-Display} konnte die Funktion des OLED-Displays einwandfrei bestätigt werden.

\section{SMD-LED}

Analog zum Blink-Beispiel-Sketch für den Test der Funktion des Mikrocontrollers (verweis Kap Beispielprogramm) wird für den Test der Funktion und der Ansteuerung der LED ein Testprogramm \ref{Code:Testprogramm für die LED} genutzt, bei dem die LED in Abständen von wenigen Sekunden zwischen der Darstellung der verschiedenen Farben (Rot, Grün und Blau) wechselt.

\begin{code}[H]
	\begin{lstlisting}[language=c++]
	int Led_Rot = 3;
	int Led_Gruen = 2;
	int Led_Blau = 5;
	
	void setup ()
	{
		pinMode (Led_Rot, OUTPUT); 
		pinMode (Led_Gruen, OUTPUT);
		pinMode (Led_Blau, OUTPUT); 
	}
	
	void loop ()
	{
		digitalWrite (Led_Rot, HIGH);
		digitalWrite (Led_Gruen, LOW);
		digitalWrite (Led_Blau, LOW);
		delay (1000);
		
		digitalWrite (Led_Rot, LOW);
		digitalWrite (Led_Gruen, HIGH);
		digitalWrite (Led_Blau, LOW);
		delay (1000);
		
		digitalWrite (Led_Rot, LOW);
		digitalWrite (Led_Gruen, LOW);
		digitalWrite (Led_Blau, HIGH);
		delay (1000);
	}
\end{lstlisting}      

\caption[Testprogramm für die LED]{Testprogramm für die LED}\label{Code:Testprogramm für die LED}    
\end{code} 

Dadurch konnte die Funktion der LED und die korrekte Ansteuerung der LED bestätigt werden.

\section{Drucktaster und Mikroschalter}

Die Funktion des Drucktasters und des Mikroschalters können auf die gleiche Art und Weise mithilfe des gleichen Testprogramms geprüft werden. Bei dem Testprogramm wird zunächst die Farbe der LED geändert, wenn der Taster oder Schalter betätigt ist, sobald der Taster oder Schalter nicht mehr betätigt wird, kehrt die LED in ihren Ursprungszustand zurück \ref{Code:Testprogramm für die Taster}.

\begin{code}[H]
	\begin{lstlisting}[language=c++]
	int Taster = 11;
	int StatusTaster = 0;
	
	void setup()
	{
		pinMode(LED_BUILTIN, OUTPUT);
		pinMode(Taster, INPUT);
		Serial.begin(9600);
	}
	
	void loop()
	{
		StatusTaster = digitalRead(Taster);
		
		if (StatusTaster == HIGH)
		{
			digitalWrite(LEDR, HIGH);
			digitalWrite(LEDG, LOW);
			digitalWrite(LEDB, LOW);
			delay(2000);
			
			digitalWrite(LEDR, LOW);
			digitalWrite(LEDG, LOW);
			digitalWrite(LEDB, HIGH);
		}
	}
\end{lstlisting}      

\caption[Testprogramm für die Taster]{Testprogramm für die Taster}\label{Code:Testprogramm für die Taster}    
\end{code} 

Sowohl der Drucktaster als auch der Mikroschalter konnten durch diesen Test ihre Funktion bestätigen. Die Umsetzung dieser Auswertung im Code für den Demonstrator erwies sich als problematisch, da der Zustand der beiden Schalter wurde nicht zuverlässig geprüft wurde. Dies konnte durch die Implementierung eines Debounce-Delays \cite{SM.2022} im Code gelöst werden \ref{Code:Testprogramm für die Taster mit Debounce}.

\begin{code}[H]
	\begin{lstlisting}[language=c++]
	int Taster = 3;
	int StatusTaster = HIGH;
	int letzterStatusTaster = HIGH;
	unsigned long letzteZeit = 0;
	unsigned long debounceDelay = 50;
	
	void setup()
	{
		pinMode(LED_BUILTIN, OUTPUT);
		pinMode(Taster, INPUT_PULLUP);
		Serial.begin(9600);
	}
	
	void loop()
	{
		int reading = digitalRead(Taster);
		
		if (reading != letzterStatusTaster) {
			letzteZeit = millis();
		}
		
		if ((millis() - letzteZeit) > debounceDelay) {
			if (reading != StatusTaster) {
				StatusTaster = reading;
				
				if (StatusTaster == LOW) {
					digitalWrite(LEDR, HIGH);
					digitalWrite(LEDG, LOW);
					digitalWrite(LEDB, LOW);
					delay(2000);
					
					digitalWrite(LEDR, LOW);
					digitalWrite(LEDG, LOW);
					digitalWrite(LEDB, HIGH);
				}
			}
		}
		letzterStatusTaster = reading;
	}
\end{lstlisting}      

\caption[Testprogramm für die Taster mit Debounce]{Testprogramm für die Taster mit Debounce}\label{Code:Testprogramm für die Taster mit Debounce}    
\end{code}

\section{Drehwinkel-Encoder}

Um die Funktion und korrekte Ansteuerung des Drehwinkel-Encoders zu testen, wird das Testprogramm \ref{Code:Testprogramm für den Encoder} verwendet. Das Programm wertet die Drehung des Encoders aus und gibt den neuen Zustand im seriellen Monitor der Arduino IDE aus \cite{Funduino.2024}.

\begin{code}[H]
	\begin{lstlisting}[language=c++]
	#include <Encoder.h>
	
	const int CLK = 9;
	const int DT = 2;
	const int SW = 3;
	long altePosition = -999;
	
	Encoder meinEncoder(DT, CLK);
	
	void setup()
	{
		Serial.begin(9600);
		pinMode(SW, INPUT);
	}
	
	void loop()
	{
		long neuePosition = meinEncoder.read();
		
		if (neuePosition != altePosition)
		{
			altePosition = neuePosition;
			Serial.println(neuePosition);
		}
		
		int StatusTaster = digitalRead(SW);
		if (StatusTaster == 0) {
			Serial.println("Switch betaetigt");
			Serial.println("Switch betaetigte");
		}
	}
\end{lstlisting}      

\caption[Testprogramm für den Encoder]{Testprogramm für den Encoder}\label{Code:Testprogramm für den Encoder}    
\end{code}

\section{Mittlere Geschwindigkeit des Schlittens}

Zur Ermittlung der mittlere Geschwindigkeit des Schlittens, ist eine Division der zurückgelegten Strecke durch die dafür benötigte Zeit erforderlich. Für die Tests wurde der Demonstrator aufgebaut und die Stufen jeweils fünfmal gefahren. Die Zeit, die der Schlitten vom Wendepunkt bis zum Wendepunkt benötigt, wurde in der jeweiligen Stufe gestoppt. Die Strecke beträgt 0,35\ m. Die Zeitmessung erfolgte mit einer handelsüblichen Stoppuhr. Die Ergebnisse sind in der Tabelle \ref{TestZeitTab} aufgeführt.

\begin{figure}[H]
\begin{center}
	\fontsize{8}{10}\selectfont
	\begin{tabularx}{\linewidth}{|p{0.8cm}|X|X|X|X|X|X|}
		\hline 
		\textbf{Stufe} & \textbf{Ergebnis Versuch 1 [s]} & \textbf{Ergebnis Versuch 2 [s]} & \textbf{Ergebnis Versuch 3 [s]}& \textbf{Ergebnis Versuch 4 [s]} & \textbf{Ergebnis Versuch 5 [s]} \\ \hline
		
		1 & 3,54 & 3,61 & 3,62 & 3,63 & 3,58 \\ \hline
		2 & 2,43 & 2,35 & 2,42 & 3,37 & 2,32 \\ \hline
		3 & 1,95 & 1,83 & 1,86 & 1,97 & 1,89 \\ \hline
		4 & 1,43 & 1,58 & 1,62 & 1,64 & 1,89 \\ \hline
		5 & 1,39 & 1,38 & 1,48 & 1,51 & 1,31 \\ \hline
		6 & 1,27 & 1,24 & 1,23 & 1,25 & 1,21 \\ \hline
		7 & 1,16 & 1,12 & 1,17 & 1,11 & 1,13 \\ \hline
		8 & 0,97 & 1,05 & 1,08 & 1,05 & 1,09 \\ \hline
		9 & 1,06 & 0,96 & 1,01 & 1,01 & 1,03 \\ \hline
		10 & 0,96 & 0,96 & 0,94 & 1,00 & 0,98 \\ \hline
		
		\end{tabularx}
			\captionof{table}{Ergebnisse Messung der Zeit eines Weges der einzelnen Stufen}
			\label{TestZeitTab}
		\end{center}
\end{figure}

Mit den Ergebnisse aus der Tabelle \ref{TestZeitTab} kann die mittlere Geschwindigkeit errechnet werden. Die Strecke dividiert mit der Zeit ergibt die mittlere Geschwindigkeit, erkenntlich in Tabelle \ref{TestMeterSekunde}. Dabei ist zu beachten dass die Ergebnisse in Meter pro Sekunde dargestellt sind. 

\begin{figure}[H]
	\begin{center}
		\fontsize{8}{10}\selectfont
		\begin{tabularx}{\linewidth}{|p{0.8cm}|X|X|X|X|X|X|}
			\hline 
			\textbf{Stufe} & \textbf{Ergebnis Versuch 1 [m/s]} & \textbf{Ergebnis Versuch 2 [m/s]} & \textbf{Ergebnis Versuch 3 [m/s]}& \textbf{Ergebnis Versuch 4 [m/s]} & \textbf{Ergebnis Versuch 5 [m/s]} & \textbf{\O [m/s]}\\ \hline
			
			1 & 0,0988 & 0,0969 & 0,0966 & 0,0964 & 0,0977 & 0,0973 \\ \hline
			2 & 0,1440 & 0,1489 & 0,1446 & 0,1476 & 0,1508 & 0,1472 \\ \hline
			3 & 0,1794 & 0,1912 & 0,1881 & 0,1776 & 0,1851 & 0,1843 \\ \hline
			4 & 0,2447 & 0,2215 & 0,2160 & 0,2134 & 0,2201 & 0,2231 \\ \hline
			5 & 0,2517 & 0,2536 & 0,2364 & 0,2317 & 0,2671 & 0,2481\\ \hline
			6 & 0,2755 & 0,2822 & 0,2845 & 0,2800 & 0,2892 & 0,2823 \\ \hline
			7 & 0,3017 & 0,3125 & 0,2991 & 0,3465 & 0,3097 & 0,3076 \\ \hline
			8 & 0,3608 & 0,3333 & 0,3240 & 0,3333 & 0,3211 & 0,3211 \\ \hline
			9 & 0,3301 & 0,3645 & 0,3465 & 0,3465 & 0,3398 & 0,3455 \\ \hline
			10 & 0,3645 & 0,3645 & 0,3723 & 0,3500 & 0,3571  & 0,3617 \\ \hline
			
		\end{tabularx}		
		\captionof{table}{Mittlere Geschwindigkeit und Durchschnittswert in SI-Einheiten}
		\label{TestMeterSekunde}
	\end{center}
\end{figure}

Da die Darstellung für in Meter pro Sekunde für Schrittmotoren unüblich sind, wurden diese mit in Millimeter pro Sekunde umgerechnet, erkenntlich in Tabelle \ref{TestMillimeterSekunde}. 

\begin{figure}[H]
	\begin{center}
		\fontsize{8}{10}\selectfont
		\begin{tabularx}{\linewidth}{|p{0.8cm}|X|X|X|X|X|X|}
			\hline 
			\textbf{Stufe} & \textbf{\O [m/s]} & \textbf{\O [mm/s]} \\ \hline
			
			1 & 0,0973 & 97,33  \\ \hline
			2 & 0,1472 & 147,2  \\ \hline
			3 & 0,1843 & 184,3  \\ \hline
			4 & 0,2231 & 223,1  \\ \hline
			5 & 0,2481 & 248,1  \\ \hline
			6 & 0,2823 & 282,3  \\ \hline
			7 & 0,3076 & 307,6  \\ \hline
			8 & 0,3345 & 334,5  \\ \hline
			9 & 0,3455 & 345,5  \\ \hline
			10 & 0,3617 & 361,7 \\ \hline
			
		\end{tabularx}		
		\captionof{table}{Durchschnittswerte umgerechnet in mm/s}
		\label{TestMillimeterSekunde}
	\end{center}
\end{figure}

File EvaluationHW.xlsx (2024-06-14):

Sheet: Report
A24-27: Demonstator für einen Schrittmotor
Short Description
Die Projektarbeit besteht im Wesentlichen darin, einen Demonstrator für einen Schrittmotor zu erstellen. Mithilfe eines Arduino Nano 33 BLE Sense Lite wird die Steuerung realisiert. Der Demonstrator soll die wesentlichen Vorzüge von Schrittmotoren abbilden können, wie der präzisen Positionierung und der diskreten Positionierung ohne weiteres Positionsfeedback. Umgesetzt wird dies durch eine Auswahl von verschiedenen Modis, die der Benutzter fahren kann. Die verschiedenen Modi repräsentieren unterschiedliche Einstellungen für Geschwindigkeit, Beschleunigung und Positionierung des Schrittmotors.
github Project
https://github.com/janterveen/A24-27-DemonstratorSchrittmotor.git
Author:
Name | Surname | Matrikelnumber | github Nickname |  | Responsible (Just one person)
ter Veen | Jan | 7022071 | janterveen |  | Maik Theilmann
Theilmann | Maik | 7021861 | MaikTh
Stein | Enno | 7021960 | ennostein
Hanneken | Lars | 7021910 | Lars2702
Grönke | Jannik | 7022006 | JannikG24
Studiengang | Maschinenbau und Design
Semester: | SoSe2024
Projektstart: | 2024-03-14
Geplantes Projektende: | 2024-06-20
Modul: | Automatisierungstechnik
CPs: | 5
Bewertung
Arbeitspaket |  |  |  | `++/+/0/-/--
 |  |  |  | 0 | 0
 |  |  |  | 0 | 0
 |  |  |  | 0 | 0
 |  |  |  | 0 | 0
 |  |  |  | 0 | 0
 |  |  |  | 0 | 0
Presentation Literature
Literature | LaTeX project |  |  |  | 5
 | completeness |  |  |  | 5
 | relevance |  |  |  | 5
 | quality |  |  |  | 5
 | presentation |  |  |  | 5
 | description |  |  |  | 5
 | key words |  |  |  | 5
 | bib file | filename "MyLiterature.bib" |  |  | 5
 |  | correct types |  |  | 5
 |  | all fields |  |  | 5
 |  | sorted (abc) |  |  | 5
 |  | label "author:year" |  |  | 5
 |  | indents |  |  | 5
 |  | empty lines |  |  | 5
 |  |  | formalities | 0
 |  |  |  | 0 | 70
Manual
Manual | Project Management | LaTeX project |  |  | 10 | Hardware
 | Contents | main function |  |  | 5
 |  | Installation |  |  | 5
 |  | first steps |  |  | 5
 |  | sketch of the GUI or UI |  |  | 10
 |  | help |  |  | 5
 |  | functions |  |  | 10
 |  | maintenance |  |  | 5
 |  | Troubleshooting |  |  | 10
 |  | specifications |  |  | 5
 | Formalities | photo of the running system on the titlepage |  |  | 5
 |  | all diagrams, sketches, pictures with tikz, minimum 5 |  |  | 10
 |  | independence of the internals |  |  | 5
 |  |  | formalities | 0
 |  |  |  | 0 | 90
Manufacturing and Assembly
Manufacturing and Assembly | Project Management | LaTeX project |  |  | 10
 | Contents | idea |  |  | 5
 |  | folder struture |  |  | 5
 |  | files |  |  | 5
 |  | hints for manufacturing |  |  | 10
 |  | description of assembly |  |  | 5
 |  |  | formalities | 0
 |  |  |  | 0 | 40
Deassembly
Deassabmle | Project Management | LaTeX project |  |  | 10
 | Contents | idea |  |  | 5
 |  | folder struture |  |  | 5
 |  | files |  |  | 5
 |  | hints for manufacturing |  |  | 10
 |  | description of assembly |  |  | 5
 |  |  | formalities | 0
 |  |  |  | 0 | 40
Poster
Poster | Project Management | LaTeX project |  |  | 10
 |  | max 20% is pictures |  |  | 8
 |  | Own Pictures |  |  | 10
 | Contents | problem's description |  |  | 5
 |  | challenges |  |  | 5
 |  | solutions |  |  | 5
 |  | results |  |  | 7
 |  |  |  | formalities | 0
 |  |  |  | 0 | 50
Report
Introduction
Introduction |  | problem's description |  |  | 5
 |  | no phrases |  |  | 5
 |  | literature |  |  | 5
 |  | challenges (with literature) |  |  | 10
 |  | solution |  |  | 10
 |  | report's structure |  |  | 5
 |  |  | formalities | 0
 |  |  |  | 0 | 40
Part domain knowledge
domain Problem | Application |  |  |  | 20
 | problem |  |  |  | 20
 |  |  | formalities | 0
 |  |  |  | 0 | 40
domain hardware | description | interfaces | using tikz |  | 20 | Hardware
Hint: every component |  | data | Quantity |  | 10
 |  |  | Quality |  | 10
 |  | constraints |  |  | 10
 |  | dimensions |  |  | 10
 |  | conclusions |  |  | 10
 |  |  | formalities | 0
 |  |  |  | 0 | 70
domain Hardware | software | os/interfaces/protocols |  |  | 10 | Hardware
 |  | data | qualitiy |  | 10
 |  |  | quantity |  | 10
 |  |  | types |  | 5
 |  |  | structure |  | 5
 |  | code with simple example |  |  | 20
 |  | constraints |  |  | 5
 |  | conclusions |  |  | 5
 |  |  | formalities | 0
 |  |  |  | 0 | 70
domain Sensor | description | interfaces |  |  | 10 | Hardware
e.g. camera, IMU |  | properties |  |  | 7
 |  | calibration |  |  | 10
 |  | data | Quantity |  | 6
 |  |  | Quality |  | 6
 |  | constraints |  |  | 7
 |  | dimensions |  |  | 7
 |  | conclusions |  |  | 7
 |  |  | formalities | 0
 |  |  |  | 0 | 60
domain sensor | software | os/interfaces/protocols |  |  | 10 | Hardware
e.g. camera, IMU |  | data | qualitiy |  | 5
 |  |  | quantity |  | 5
 |  |  | types |  | 5
 |  |  | structure |  | 5
 |  | calibration |  |  | 10
 |  | code with simple example |  |  | 10
 |  | constraints |  |  | 5
 |  | conclusions |  |  | 5
 |  |  | formalities | 0
 |  |  |  | 0 | 60
Tests | hardware | functions |  |  | 20
 |  | parts |  |  | 20
 |  | documentation |  |  | 20
 |  |  | formalities | 0
 |  |  |  | 0 | 60
Tests | software | functions |  |  | 10
 |  | classes |  |  | 10
 |  | parts |  |  | 10
 |  | documentation |  |  | 10
 |  | automation |  |  | 10
 |  |  | formalities | 0
 |  |  |  | 0 | 50
domain system | Hardware | description |  |  | 10 | Hardware
complete system |  | design |  |  | 10
 |  | Circuit diagram |  |  | 10
 |  | interfaces |  |  | 6
 |  | properties |  |  | 6
 |  | calibration |  |  | 10
 |  | data | Quantity |  | 6
 |  |  | Quality |  | 6
 |  | constraints |  |  | 6
 |  | dimensions |  |  | 5
 |  | conclusions |  |  | 5
 |  |  | formalities | 0
 |  |  |  | 0 | 80
domain system | software | os/interfaces/protocols |  |  | 10
complete system |  | installation |  |  | 5
 |  | configuration |  |  | 5
 |  | data | qualitiy |  | 5
 |  |  | quantity |  | 5
 |  |  | types |  | 5
 |  |  | structure |  | 5
 |  | constraints |  |  | 5
 |  | conclusions |  |  | 5
 |  |  | formalities | 0
 |  |  |  | 0 | 50
Test System |  | functions |  |  | 20
 |  | parts |  |  | 20
 |  | documentation |  |  | 20
 |  |  | formalities | 0
 |  |  |  | 0 | 60
Domain Tools
Development Environment |  | Version |  |  | 5 | Hardware
e.g. Arduino IDE |  | Description |  |  | 10
e.g. OS Linux |  | Installation |  |  | 10
 |  | Configuration |  |  | 5
 |  | First Steps (description of the GUI/UI) |  |  | 5
 |  | Program "Hello World"/bash files |  |  | 5
 |  |  | formalities | 0
 |  |  |  | 0 | 40
Part methodology
methodology |  | e.g. KDD process |  |  | 5
 |  | other
 |  | Justification |  |  | 2
 |  |  |  |  | 7
Part Application Development
Documentation developer | structure |  |  |  | 10
 | idea |  |  |  | 10
 | flow chart of each step in the development, not code |  |  |  | 10
 |  |  | formalities | 0
 |  |  |  | 0 | 30
Documentation developer | structure |  |  |  | 10
 | idea |  |  |  | 5
 | flow chart of each step in the development, not code |  |  |  | 5
 | notation |  |  |  | 5
 | complettness |  |  |  | 5
 | program | readable |  |  | 5
 |  | structure/modules |  |  | 5
 |  | parameter handling |  |  | 20
 |  | error handling |  |  | 20
 |  | Message handling |  |  | 20
 |  | names | folders |  | 3
 |  |  | files |  | 3
 |  |  | modules |  | 3
 |  |  | functions |  | 3
 |  |  | variables |  | 3
 |  |  | formalities | 0
 |  |  |  | 0 | 115
Evaluation | concept |  |  |  | 5
 | Application |  |  |  | 10
 | results |  |  |  | 10
Validation | General |  |  |  | 5
 | 3 Ideas |  |  |  | 15
Conclusion |  | todo |  |  | 5
 |  | unanswered points |  |  | 5
 |  | next steps |  |  | 5
 |  |  | formalities | 0
 |  |  |  | 0 | 45
General aspects | complete |  |  |  | 5
 | thinking in components/modules |  |  |  | 25
 | adequate |  |  |  | 5
 | scope | all aspects |  |  | 5
 |  | relevance |  |  | 5
 | images | own |  |  | 5
 |  | quality |  |  | 5
 |  | enough |  |  | 5
 |  | labelled |  |  | 5
 |  | description |  |  | 5
 |  |  | formalities | 0
 |  |  |  | 0 | 70
Part Application Appendix
list of materials | list of materials | name |  | 0 | 4 | Hardware
 |  | picture |  | 0 | 4
 |  | description |  | 0 | 5
 |  | link |  | 0 | 4
 |  | prices |  | 0 | 4
 |  | complete |  | 0 | 4
 |  |  | formalities | 0
 |  |  |  | 0 | 25
List of Packages, Tools,… |  | complettness |  |  | 5
 |  | minimal |  |  | 5
 |  | documentation |  |  | 5
 |  |  | formalities | 0
 |  |  |  | 0 | 15
General Aspects
Given documentation | use of |  |  |  | 10
 | same notation |  |  |  | 10
 | Supplements |  |  |  | 10
 | same structure |  |  |  | 10
Improvements
 | Minor changes |  |  |  | 5
 | list of minor changes |  |  |  | 15
 | major improvements |  |  |  | 20
 | documentation of the major improvements |  |  |  | 5
Tranlations | 1-1 translation |  |  |  | 5
 | rewrite as an engineer |  |  |  | 15
 | rewrite as an engineer with improvements |  |  |  | 15
 |  |  | formalities | 0
 |  |  |  | 0 | 120
Project Management
Process | project plan | Allocation of tasks identifiable |  |  | 2
 |  | Plausible |  |  | 2
 |  | Results checkable |  |  | 2
 |  | Reasonable structure |  |  | 2
 | structure |  |  |  | 5
 | spelling/punctuation/grammar |  |  |  | 5
 |  |  | formalities | 0
 |  |  |  | 0 | 18
readme | Problem's description |  |  |  | 3
 | pictures |  |  |  | 4
 | Folder structure |  |  |  | 4
 | description of the folders |  |  |  | 4
 | links to folder |  |  |  | 4
 | description of the files |  |  |  | 4
 | links to files |  |  |  | 4
 |  |  | formalities | 0
 |  |  |  | 0 | 27
author.xlsx | group members |  |  |  | 3 | Hardware
 | problem's description |  |  |  | 5
 | addresses |  |  |  | 3
 | emails |  |  |  | 3
 | contact data |  |  |  | 3
 |  |  | formalities | 0
 |  |  |  | 0 | 17
project management - files |  | filenames | not short, not long |  | 5
 |  |  | only letters, no blanks,… |  | 5
 |  |  | plausible, not 1.*,… |  | 5
 |  | file headers | author |  | 5
 |  |  | project |  | 5
 |  |  | filename |  | 5
 |  |  | short description |  | 5
 |  |  | dependicies |  | 5
 |  |  |  | 0 | 40
Presentation of the results
Presentation | Project Management | LaTeX project |  |  | 10
 |  | own pictures/tikz |  |  | 10
 | Contents | Problem's description |  |  | 5
 |  | Description of the application |  |  | 5
 |  | challenges |  |  | 5
 |  | own solutions |  |  | 5
 |  | Results |  |  | 5
 |  |  | formalities | 0
 |  |  |  | 0 | 45
HTML-Software Documentation
Software Documentation | main page |  |  | 0 | 10
with Doxygen | descriptions | functions |  | 0 | 10
 |  | parameters |  | 0 | 10
 |  |  | formalities | 0
 |  |  |  | 0 | 30
 |  | Subtotal |  | 0 | 1240
 |  | Mandatory requirements |  | -1240
 |  | Total |  | -1240
 |  | Prozent |  | -100%
 |  |  |  | 0 | 339 |  | 0.00%
 |  |  |  | 0 | 380 |  | 0.00%
 |  |  |  | 0 | 395 |  | 0.00%
 |  |  |  | 0 | 420 |  | 0.00%
 |  |  |  |  | Percent | Grade
 |  |  | Grades |  |  | n.b.
 |  |  |  |  | 45 | 4
 |  |  |  |  | 50 | 3.7
 |  |  |  |  | 55 | 3.3
 |  |  |  |  | 60 | 3
 |  |  |  |  | 65 | 2.7
 |  |  |  |  | 70 | 2.3
 |  |  |  |  | 75 | 2
 |  |  |  |  | 80 | 1.7
 |  |  |  |  | 85 | 1.3
 |  |  |  |  | 90 | 1
 |  |  |  | Maximum Score
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

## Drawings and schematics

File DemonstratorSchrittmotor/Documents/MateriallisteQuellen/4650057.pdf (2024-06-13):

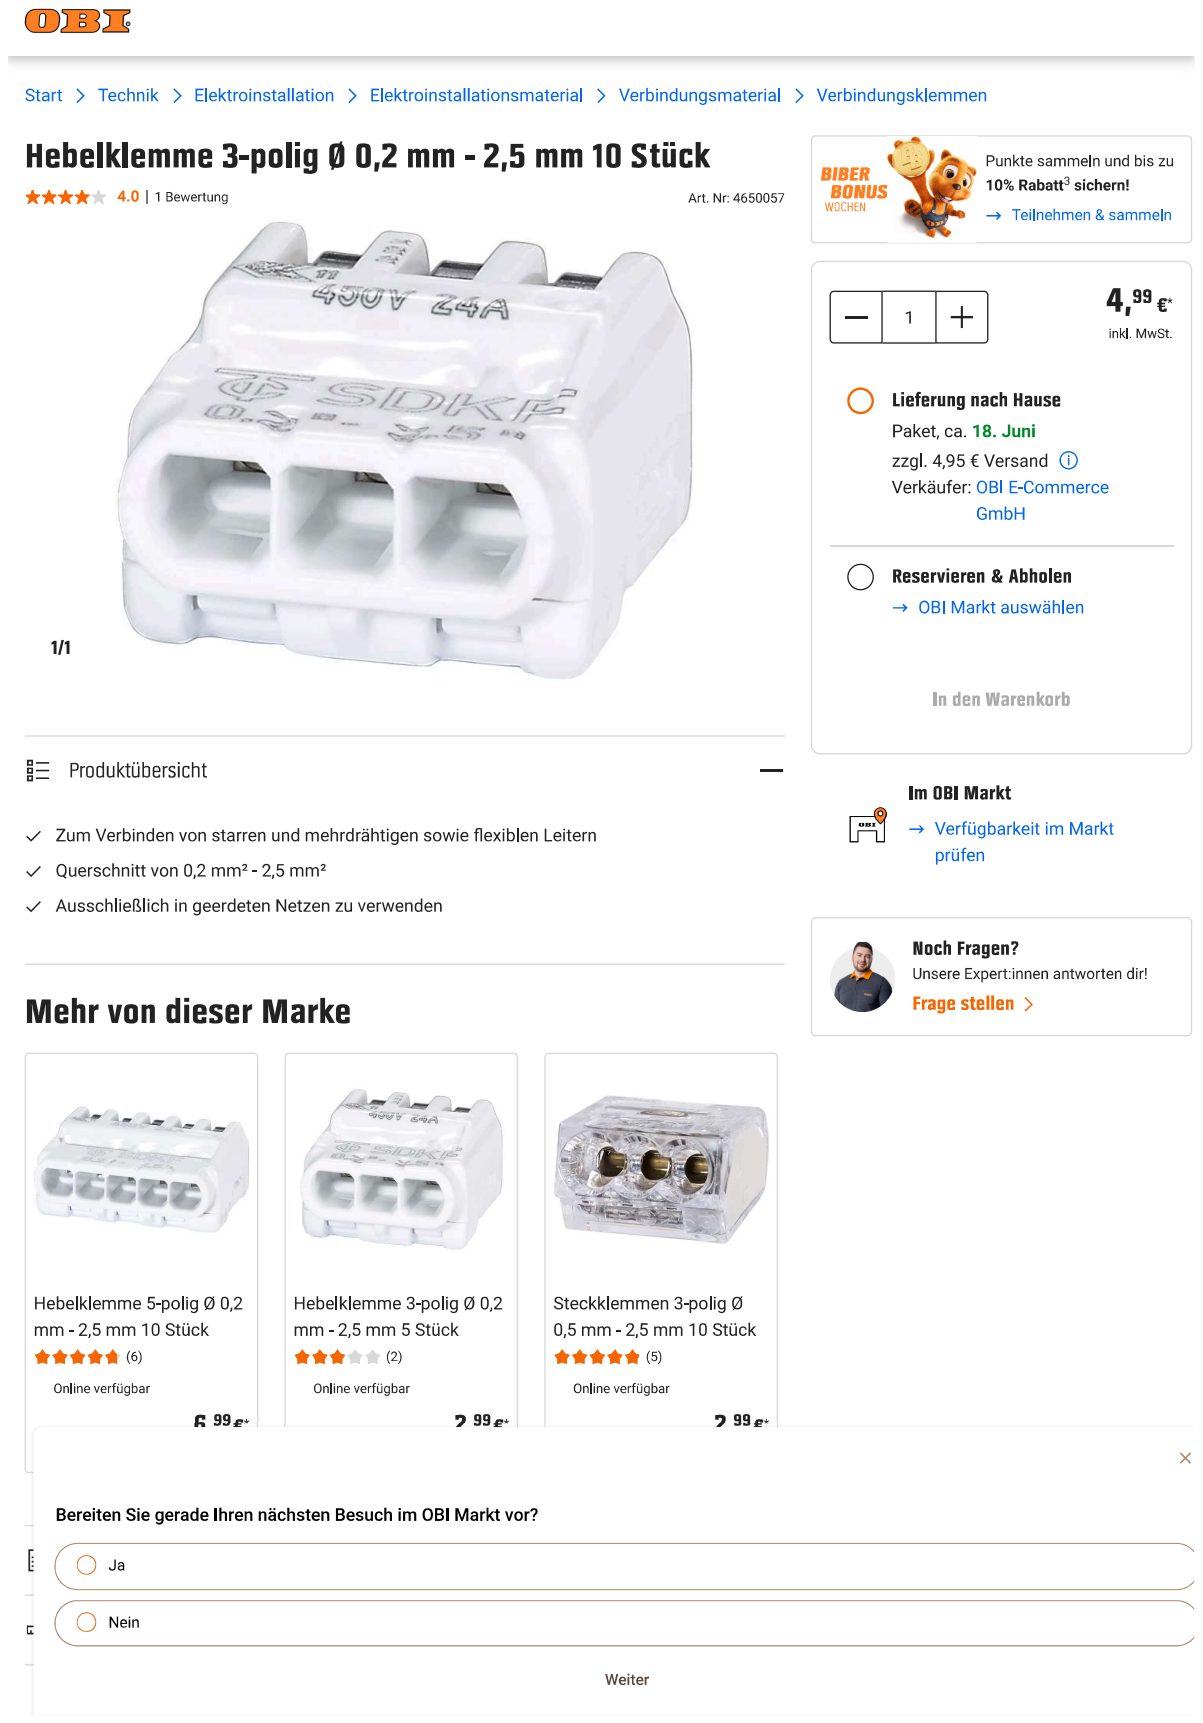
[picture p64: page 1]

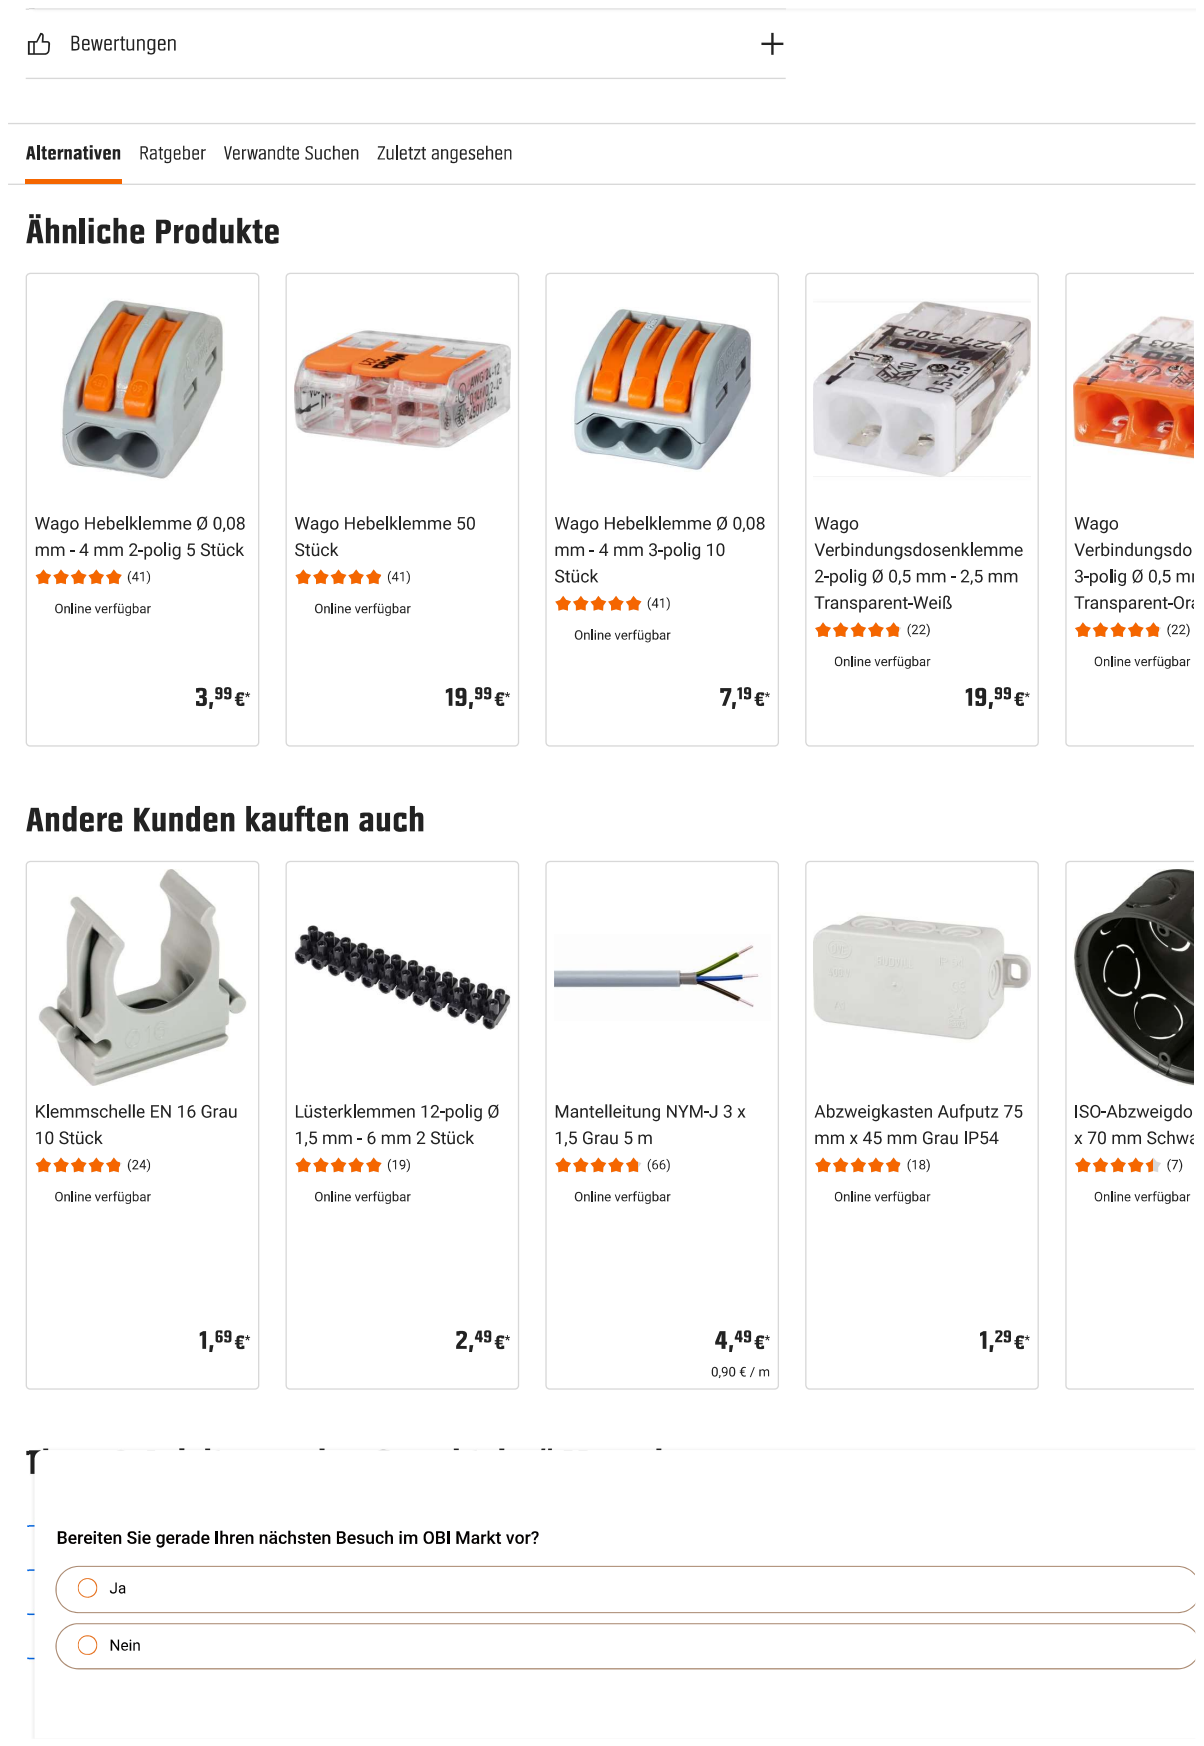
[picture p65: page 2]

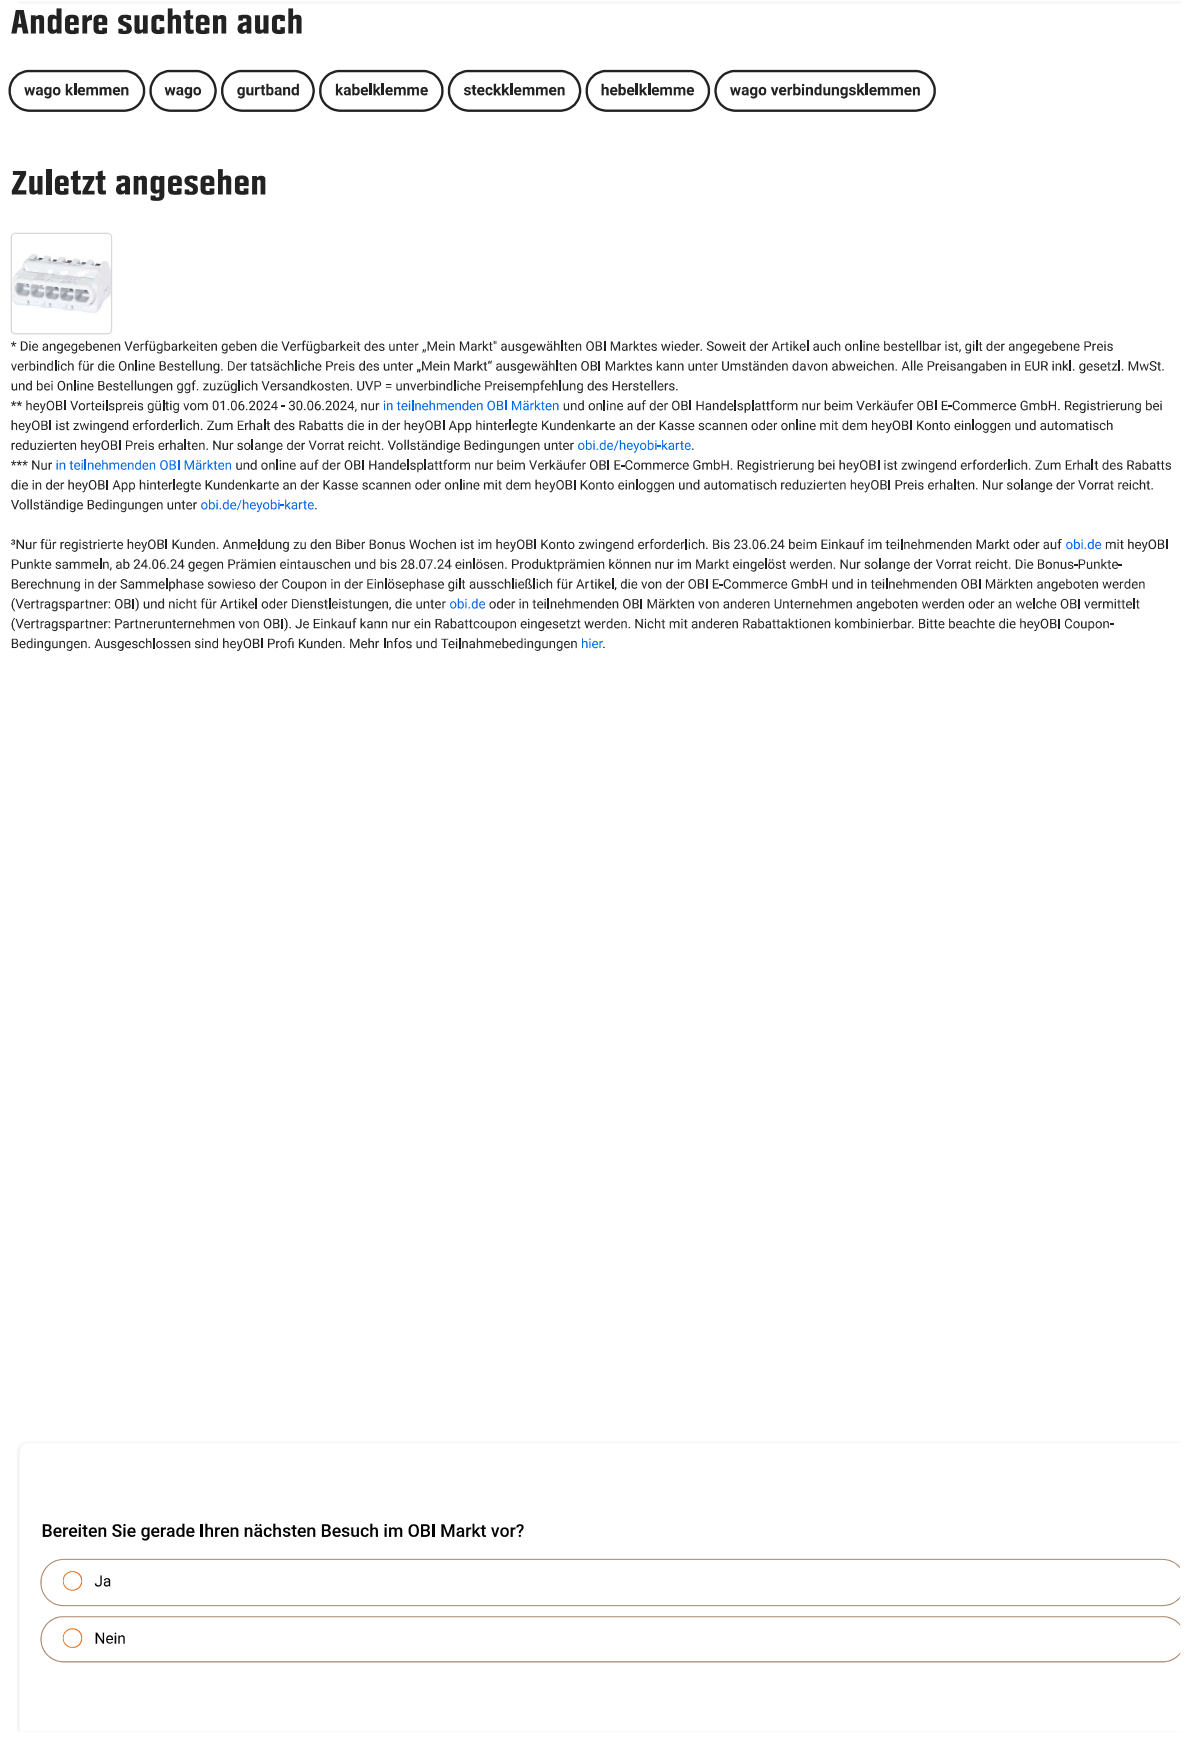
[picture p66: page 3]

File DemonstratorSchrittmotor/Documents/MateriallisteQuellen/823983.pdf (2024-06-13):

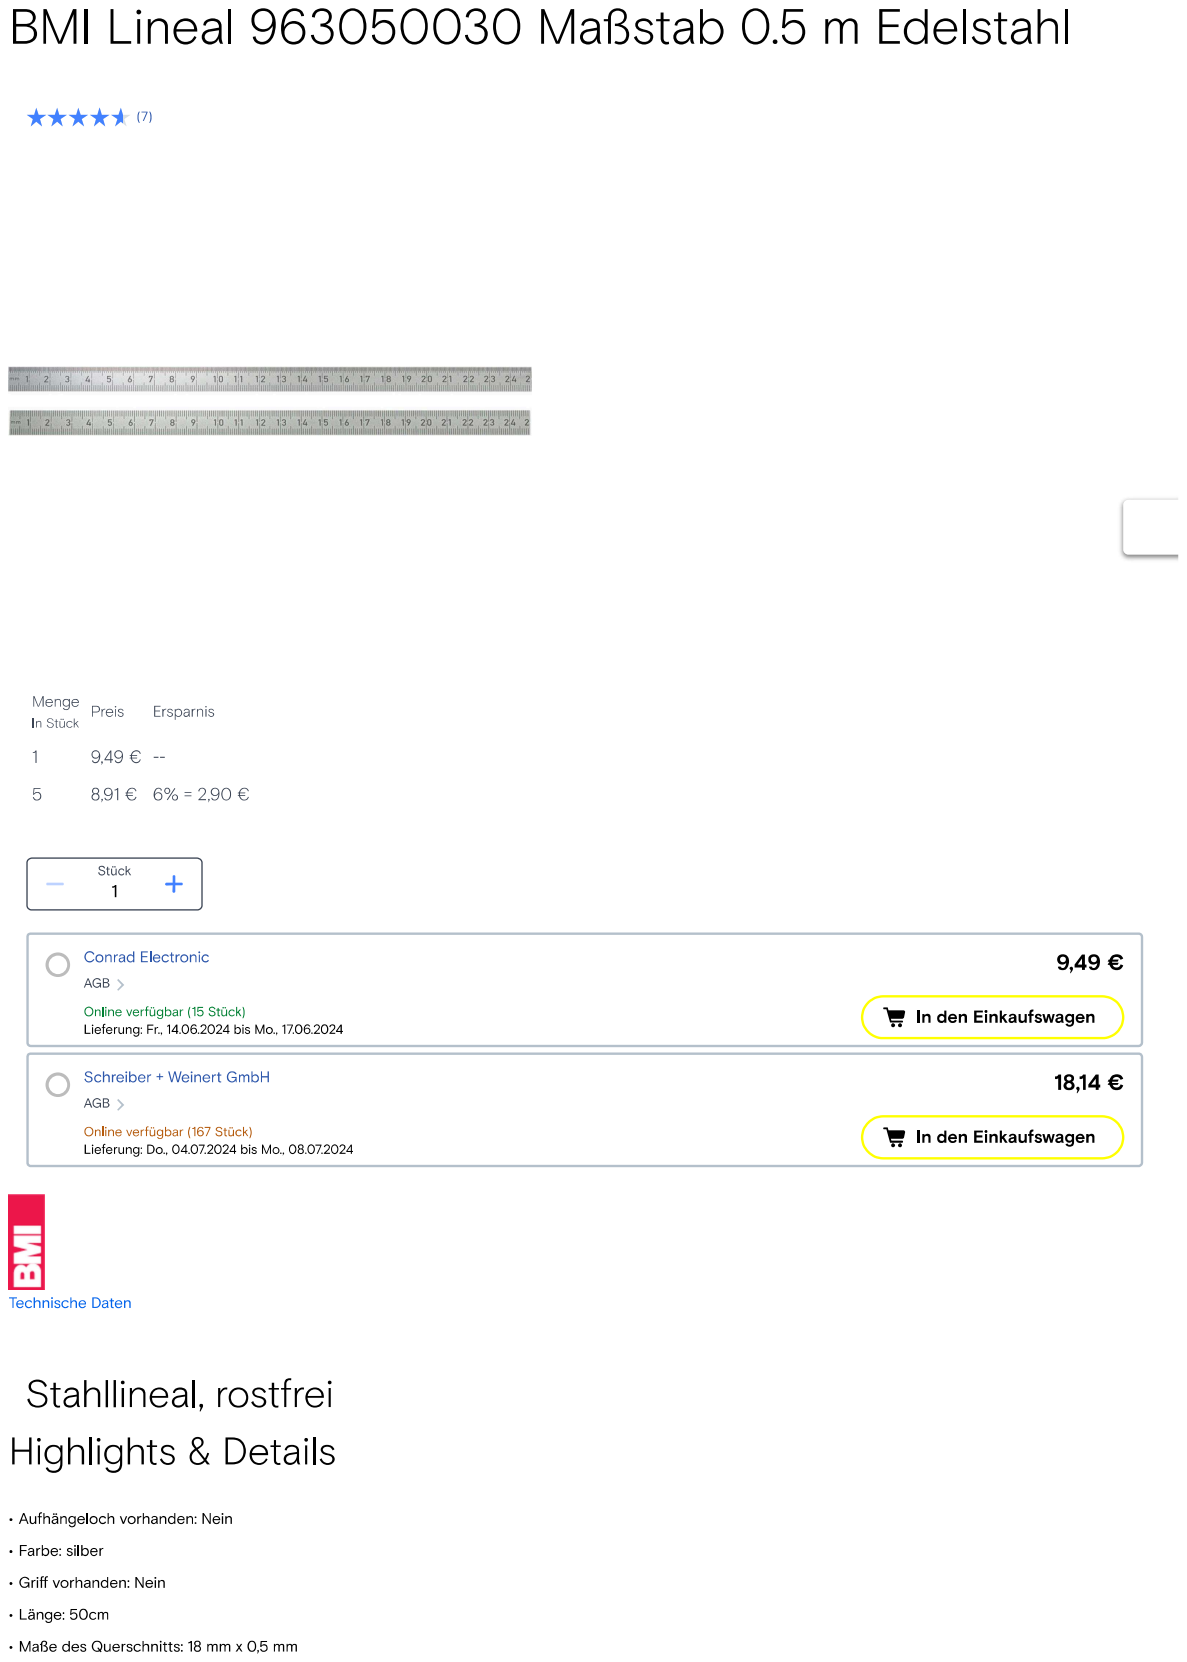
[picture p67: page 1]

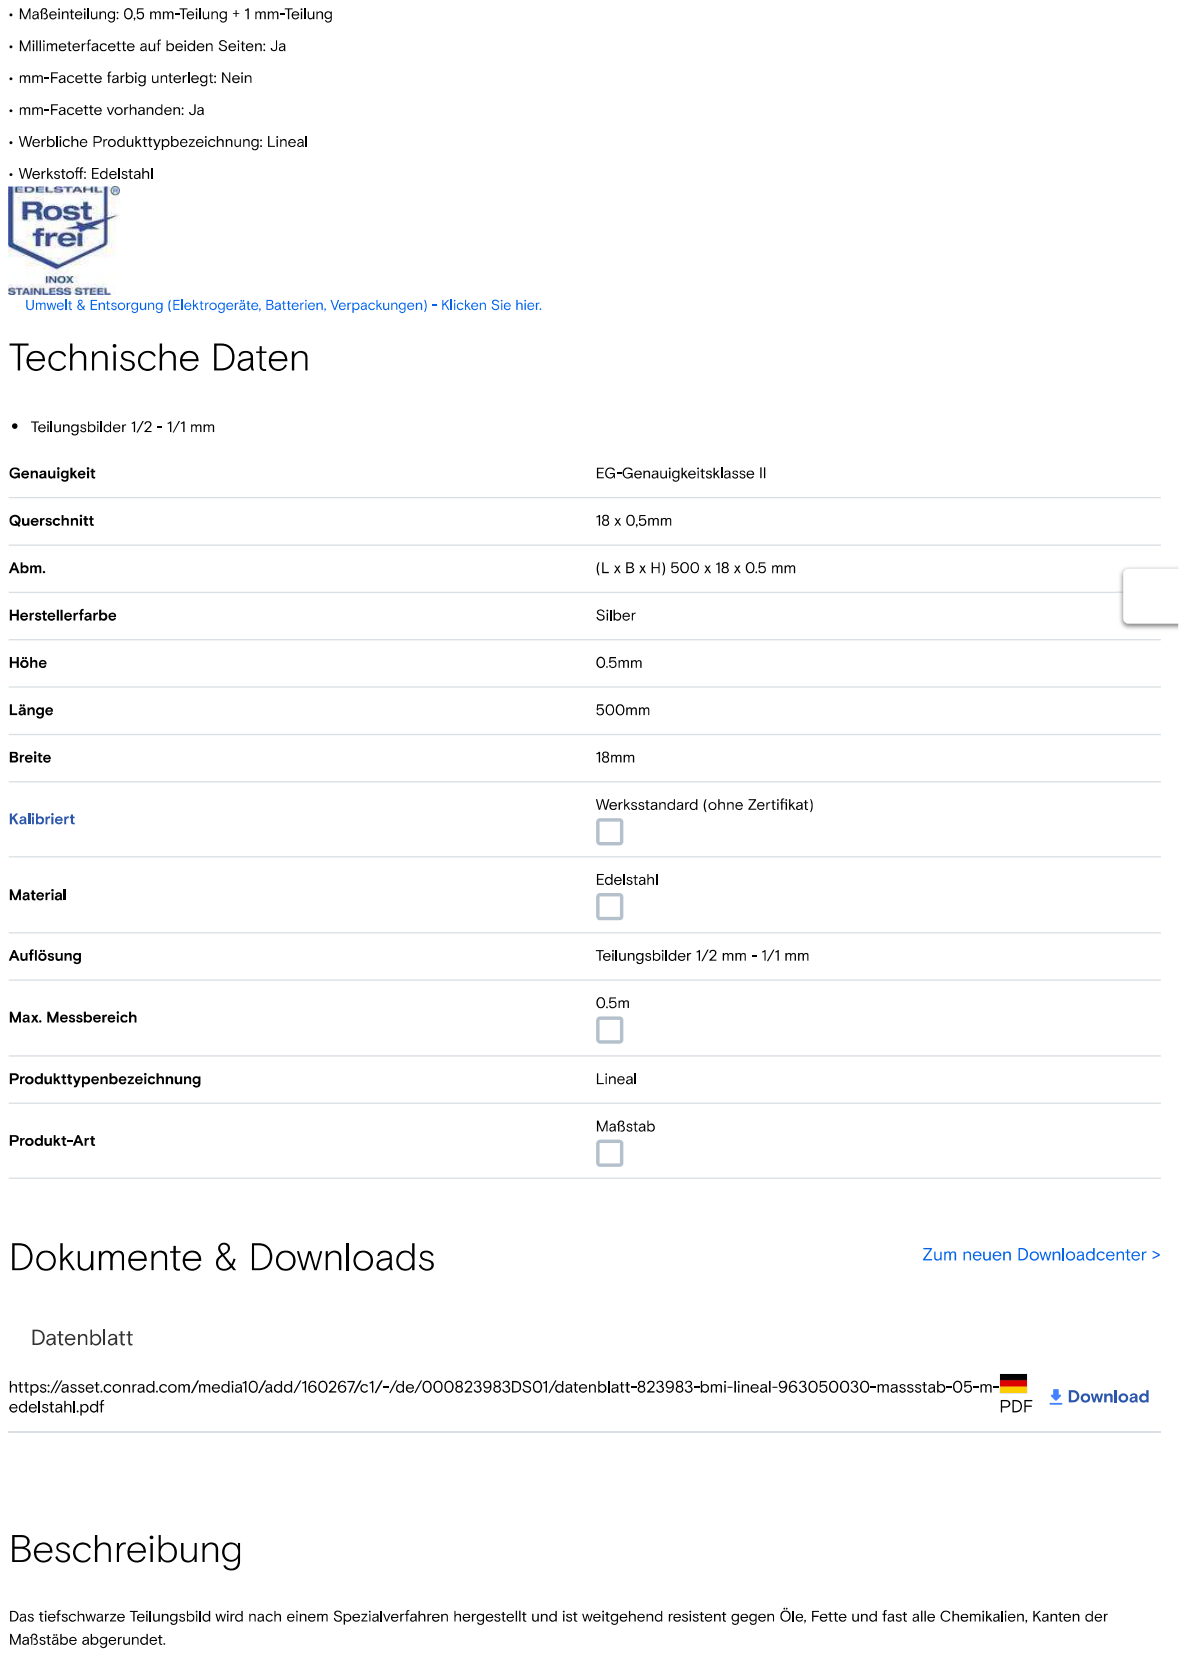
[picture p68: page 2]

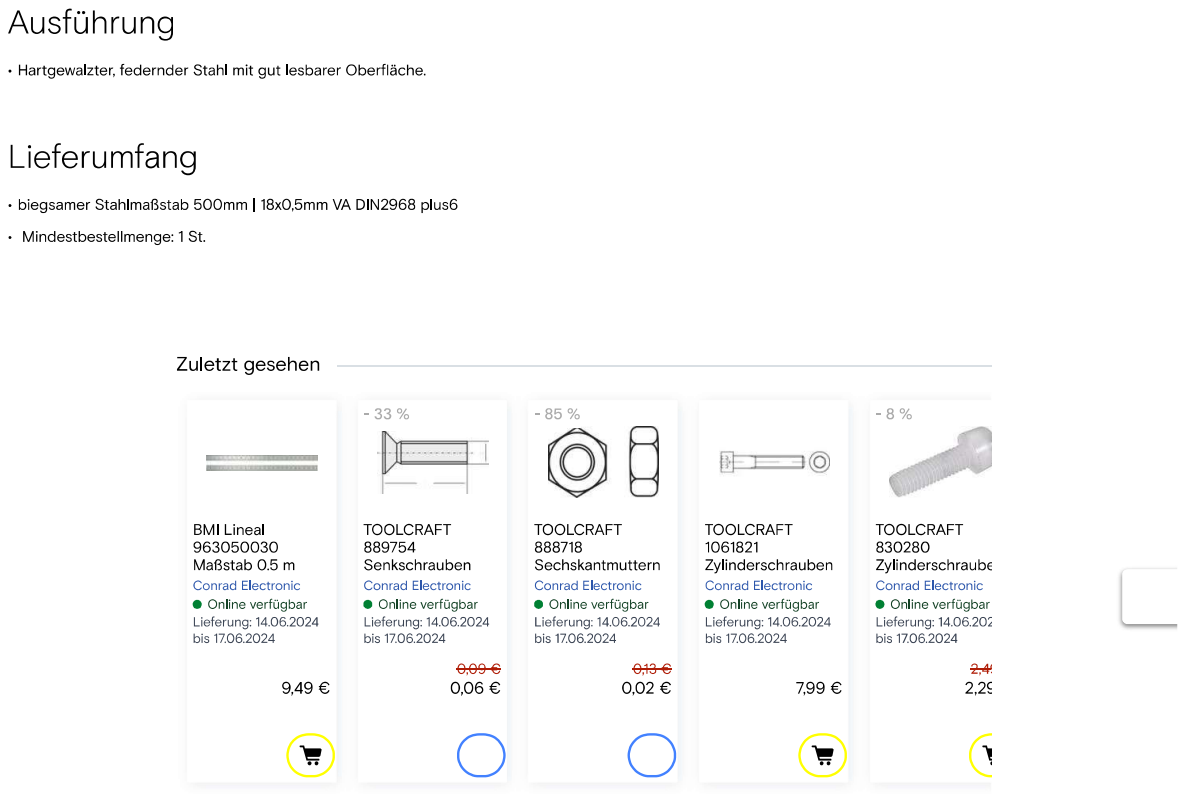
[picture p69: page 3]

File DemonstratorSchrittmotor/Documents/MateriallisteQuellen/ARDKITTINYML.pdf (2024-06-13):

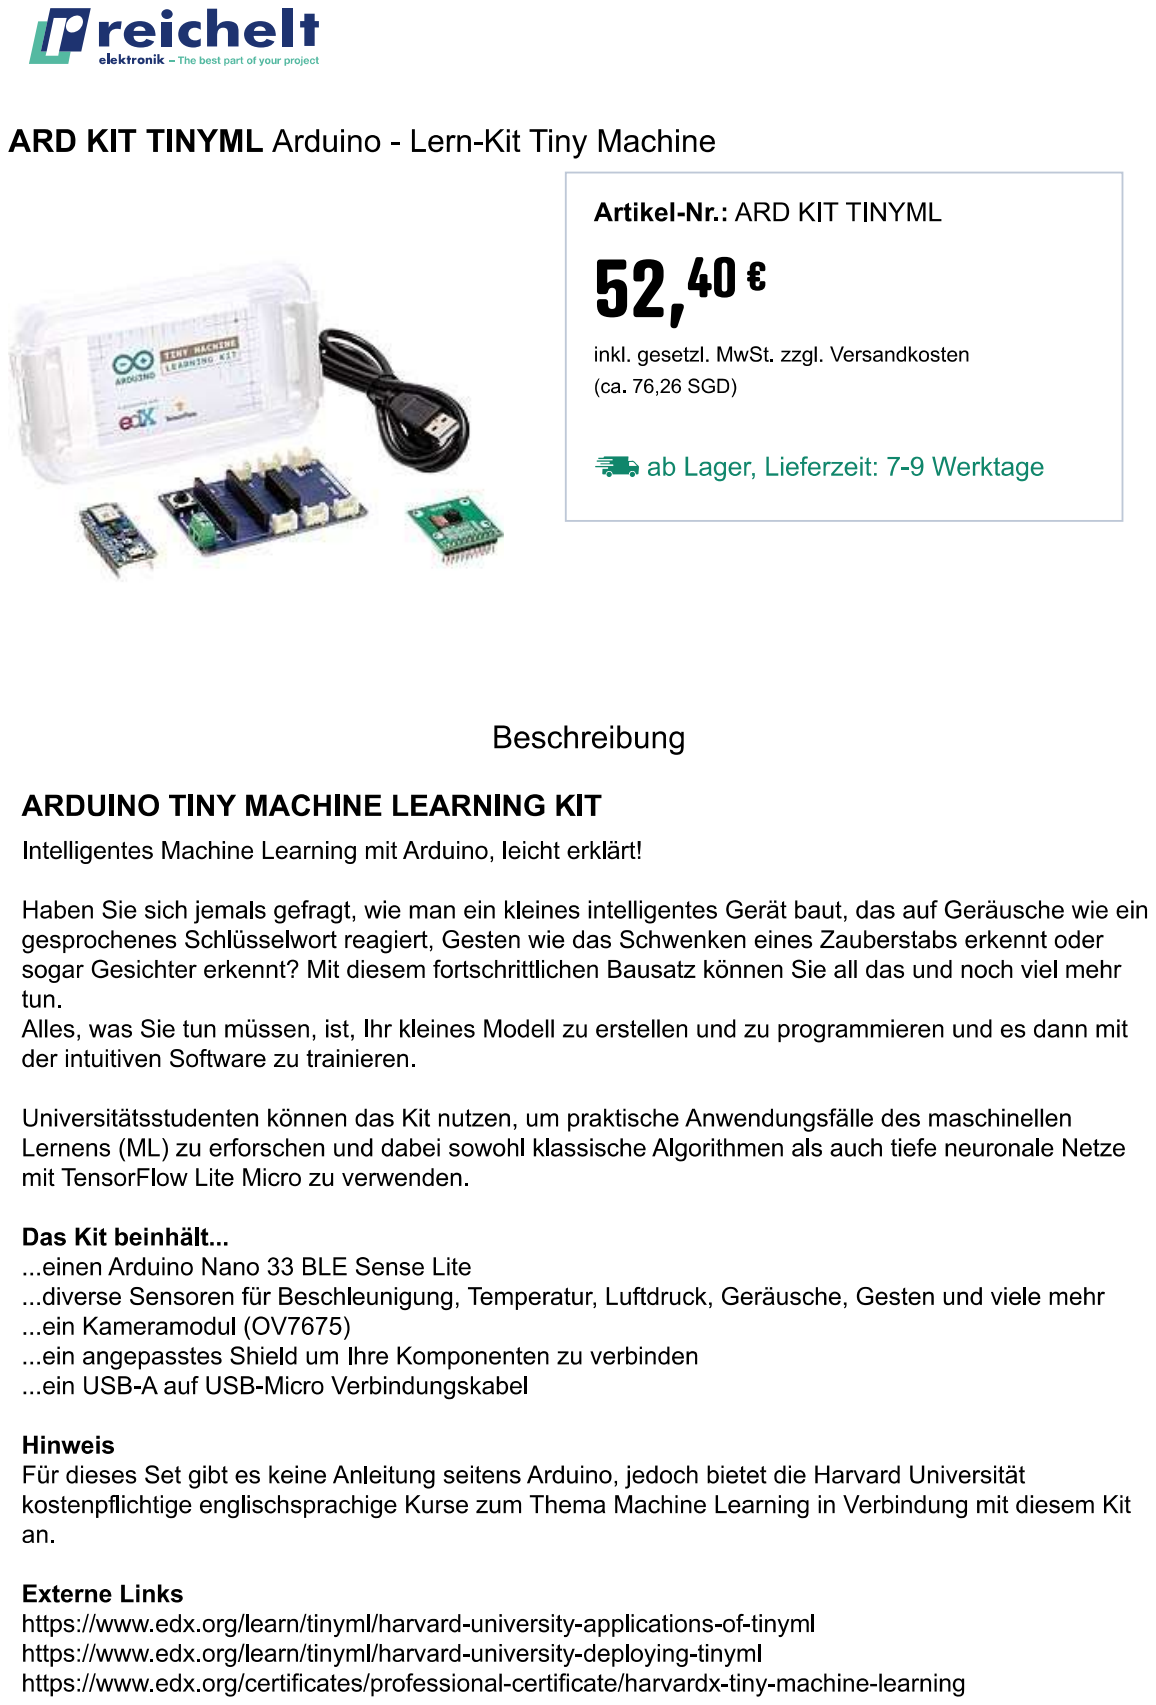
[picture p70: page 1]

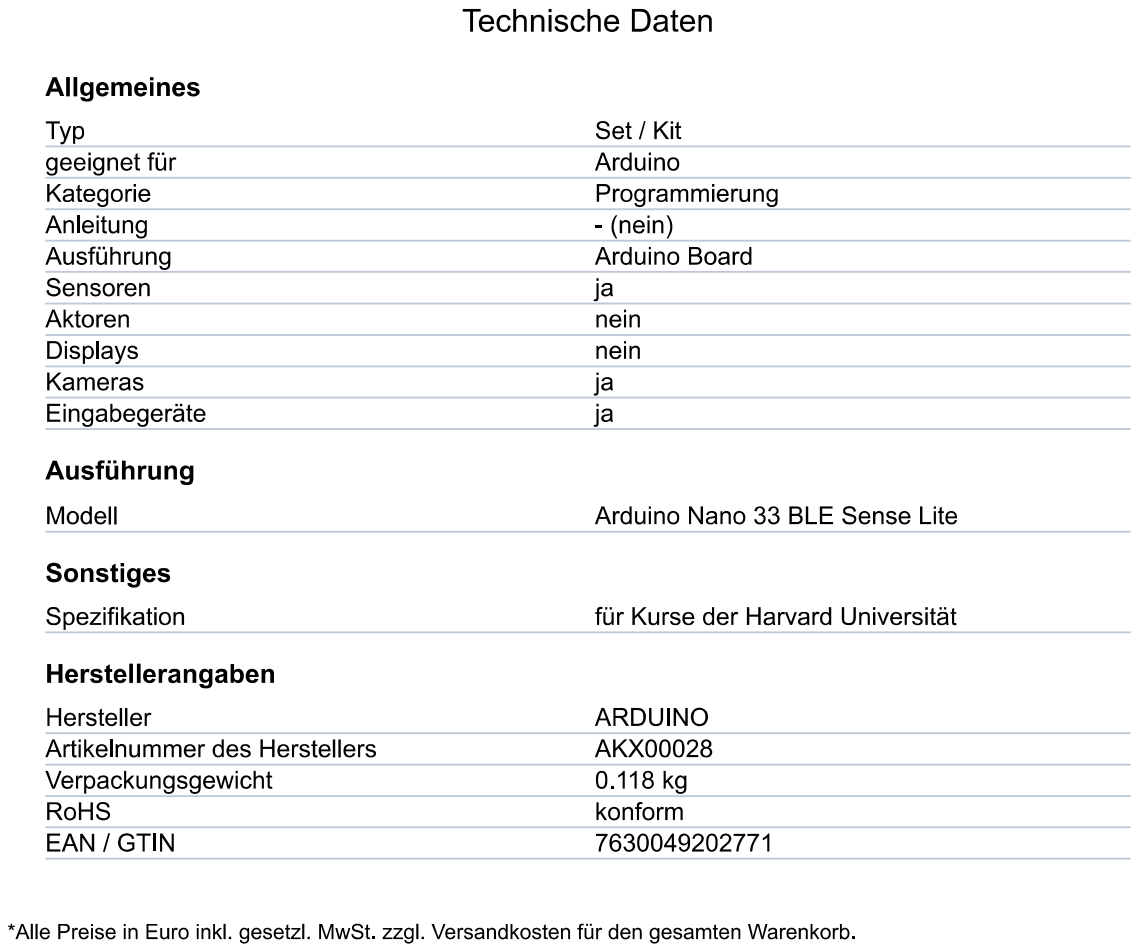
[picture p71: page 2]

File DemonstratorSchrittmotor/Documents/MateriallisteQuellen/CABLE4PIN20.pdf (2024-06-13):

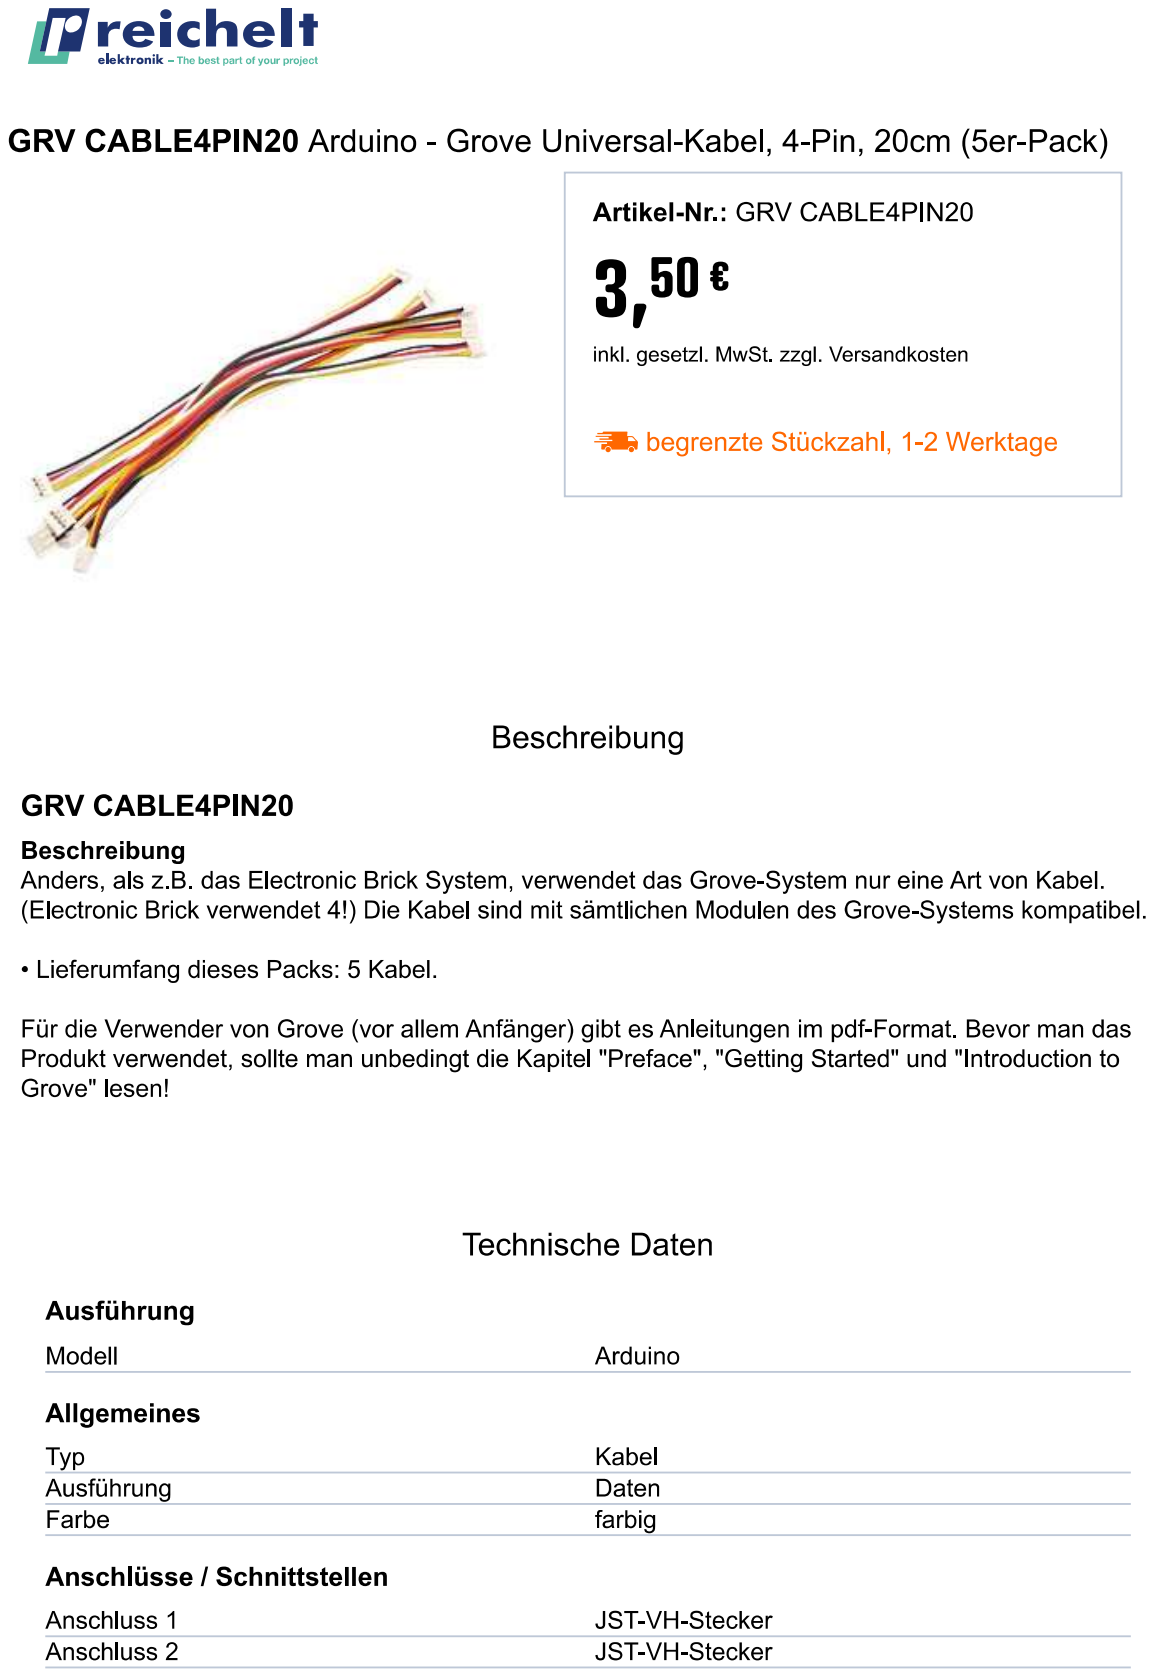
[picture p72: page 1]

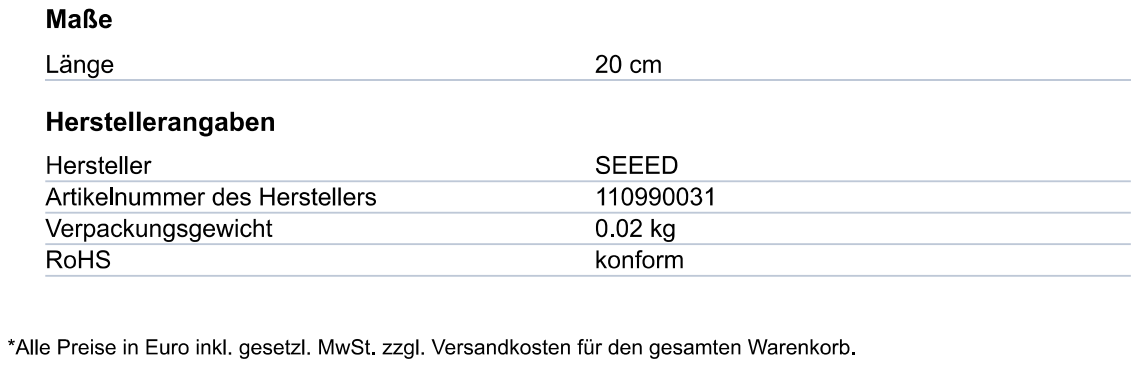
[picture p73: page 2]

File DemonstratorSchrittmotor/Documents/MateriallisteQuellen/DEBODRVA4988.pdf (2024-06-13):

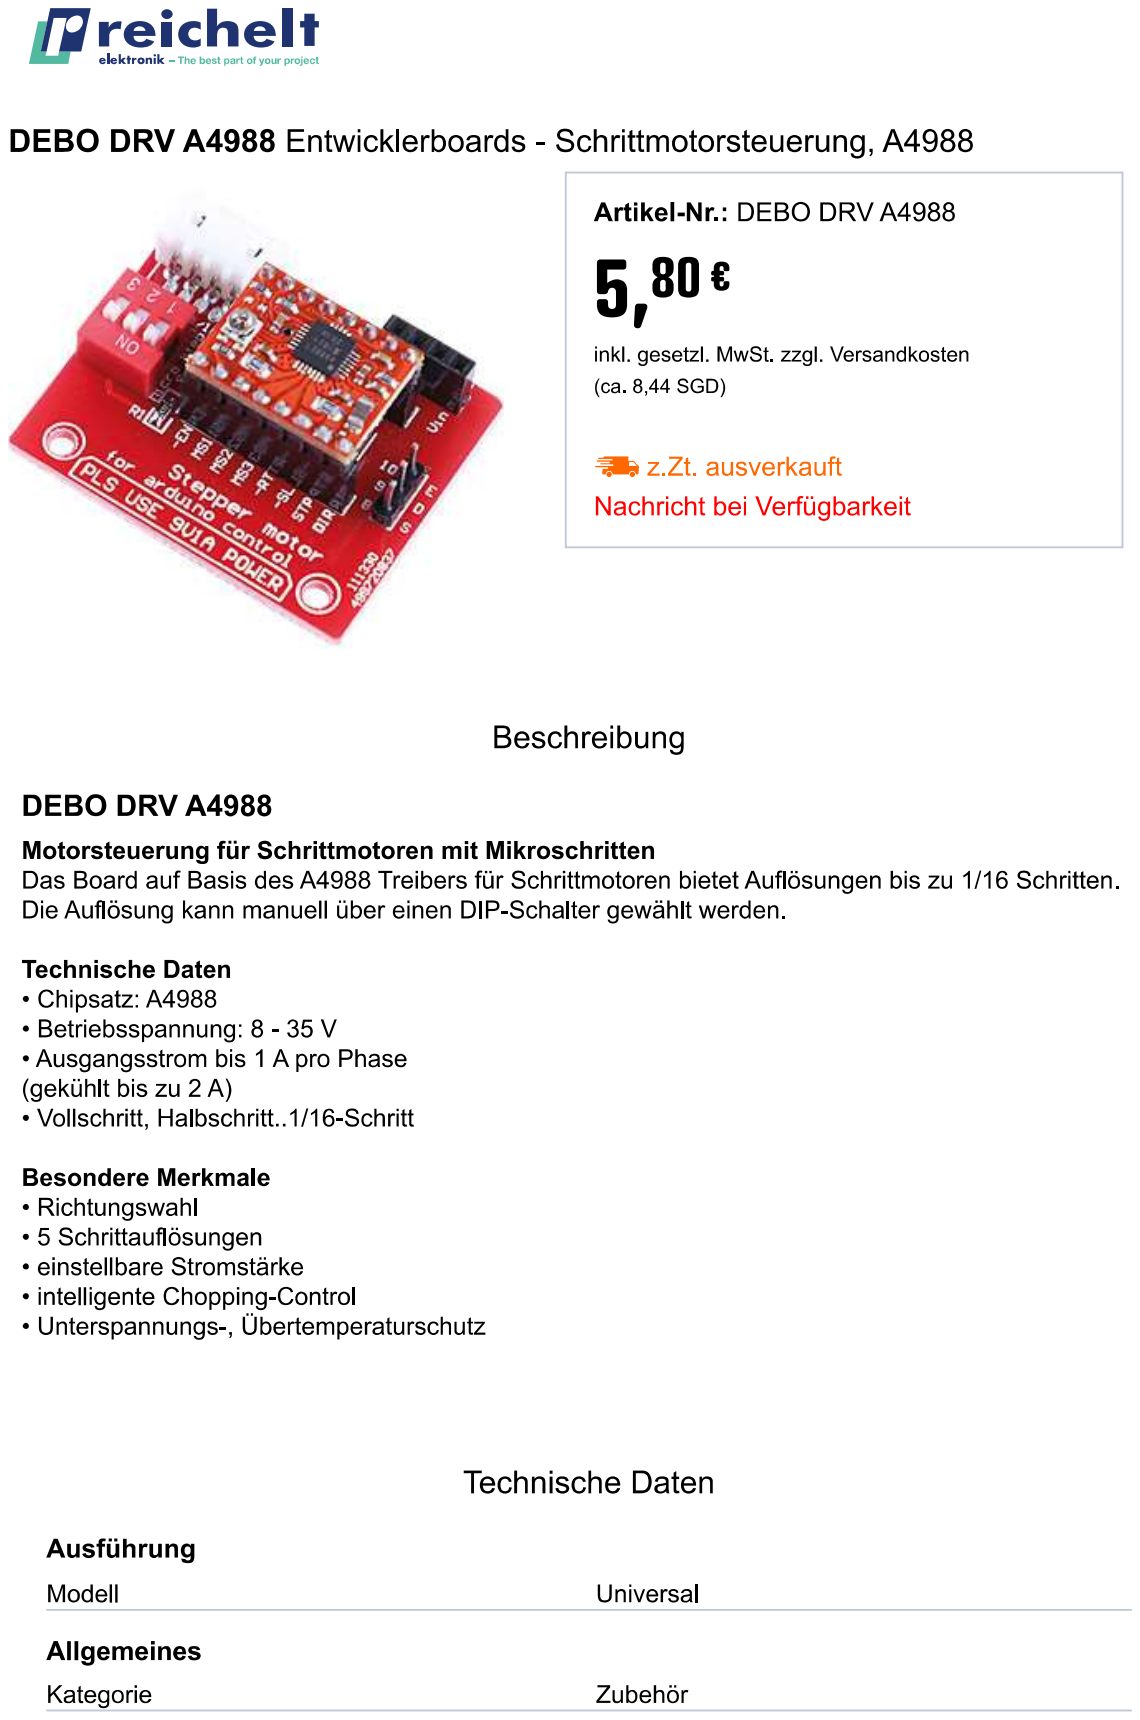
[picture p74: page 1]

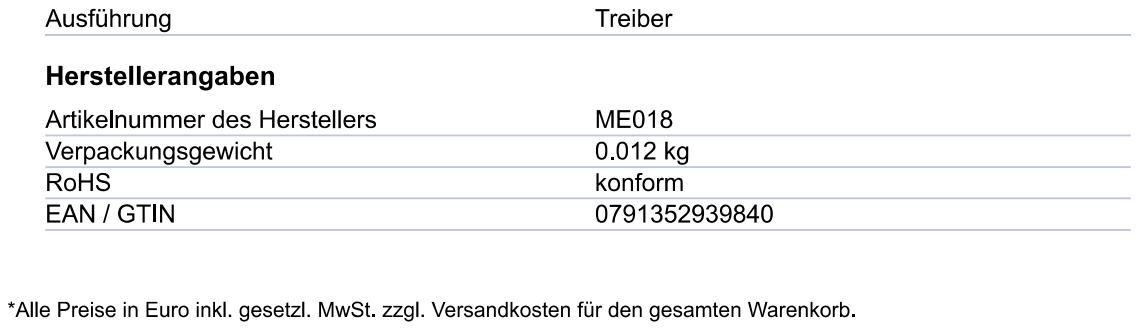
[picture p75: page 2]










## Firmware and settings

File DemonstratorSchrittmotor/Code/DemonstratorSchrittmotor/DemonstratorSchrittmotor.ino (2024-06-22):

/**@file */

/**
 * @brief Demonstration eines Stepper-Motors mit Encoder und OLED-Anzeige
 * 
 * Dieses Programm steuert einen Stepper-Motor über einen Encoder und zeigt Informationen auf einem OLED-Display an.
 * Es beinhaltet auch Taster- und Endschalter-Funktionalitäten.
 */


#include "AccelStepper.h" ///< Bibliothek für den Stepper-Motor
#include <SPI.h> ///< Bibliothek für die Kommunikation mit Displays
#include <Wire.h> ///< Bibliothek für die Kommunikation über das I2C-Protokoll
#include <Adafruit_GFX.h> ///< Bibliothek für viele Grafikfunktionen und Operationen für Displays
#include <Adafruit_SSD1306.h> ///< Bibliothek für die Ansteuerung von OLEDs mit SSD1306-Treiber
#include <Encoder.h> ///< Bibliothek für den Encoder

#define MOTOR_INTERFACE_TYPE 1 ///< Festlegung der Anbindung des Stepper-Motors, 1 bedeutet, dass der Motor über einen Treiber angeschlossen ist
#define SCREEN_WIDTH 128 ///< Festlegung der Breite des Displays
#define SCREEN_HEIGHT 64 ///< Festlegung der Höhe des Displays
#define OLED_RESET -1 ///< Festlegung des OLED-Resets
#define SCREEN_ADDRESS 0x3C ///< Festlegung der I2C-Adresse des Displays

#define PIN_STEP_DIR 4 ///< Verknüpfter digitaler Pin am Direction-Pin des Motortreibers 
#define PIN_STEP_STEP 5 ///< Verknüpfter digitaler Pin am Step-Pin des Motortreibers 
#define PIN_LED_RED 6 ///< Verknüpfter digitaler Pin am roten Kabel der LED
#define PIN_LED_GREEN 3 ///< Verknüpfter digitaler Pin am grünen Kabel der LED
#define PIN_LED_BLUE 9 ///< Verknüpfter digitaler Pin am blauen Kabel der LED
#define PIN_BUTTON 11 ///< Verknüpfter digitaler Pin am Taster
#define PIN_ENDSTOP 12 ///< Verknüpfter digitaler Pin am Endschalter
#define PIN_CLK 9 ///< Verknüpfter digitaler Pin am CLK-Pin des Encoders
#define PIN_DT 2 ///< Verknüpfter digitaler Pin am DT-Pin des Encoders
#define PIN_SW 3 ///< Verknüpfter digitaler Pin am SW-Pin des Encoders

AccelStepper stepper(MOTOR_INTERFACE_TYPE, PIN_STEP_STEP, PIN_STEP_DIR); ///< Definition des Stepper-Motors
Adafruit_SSD1306 display(SCREEN_WIDTH, SCREEN_HEIGHT, &Wire, OLED_RESET); ///< Definition des Displays
Encoder encoder(PIN_DT, PIN_CLK); ///< Definition des Encoders

int buttonStatus = HIGH; ///< Aktueller Status des Tasters (gedrückt oder nicht gedrückt)
int lastButtonStatus = HIGH; ///< Letzter Status des Tasters (gedrückt oder nicht gedrückt)
unsigned long lastDebounceTime = 0; ///< Die letzte Zeit, zu der der Taster gedrückt wurde
unsigned long debounceDelay = 50; ///< Eine Verzögerung für die Abfrage der Schalter, um die mechanischen Schwingungen auszugleichen
int endstopStatus = HIGH; ///< Aktueller Status des Endtasters (gedrückt oder nicht gedrückt)
int lastEndstopStatus = HIGH; ///< Letzter Status des Tasters (gedrückt oder nicht gedrückt)
unsigned long lastEndstopDebounceTime = 0; ///< Die letzte Zeit, zu der der Endschalter gedrückt wurde
int stage = 0; ///< Die Stufe, die für die Demonstration eingestellt ist
int speeds[] =        {1000, 1000,  500, 2000, 3500, 2000, 2000, 2000, 2000, 500, 3500}; ///< Geschwindigkeiten für jede Stufe
int accelerations[] = {1000, 2000, 2000, 2000, 2000,  300, 1000, 4000, 7000, 300, 7000}; ///< Beschleunigungen für jede Stufe
long oldPosition = -999; ///< Alte Position des Encoders für den Abgleich. Es ist nötig, dass ein Wert vorher eingestellt ist für die Funktion des Programms
const int safeSteps = 70; ///< Anzahl der Schritte, die als Sicherheitsabstand zum Endschalter gehalten werden
const int trackLength = 1750; ///< Anzahl der Schritte, die bis zum Ende der Bahn durchgeführt werden können

const char* stageMessages[] = {"Keine Stufe eingestellt", "Stufe 1", "Stufe 2", "Stufe 3", "Stufe 4", "Stufe 5", "Stufe 6", "Stufe 7", "Stufe 8", "Stufe 9", "Stufe 10"}; ///< Anzeige der eingestellten Stufe auf dem Display
const char* messages[] = {"Start...", "Startbereit", "Programm wird ausgefuehrt...", "Vorgang abgebrochen, das Geraet muss neu gestartet werden", ""}; ///< Nachricht auf dem Display

/**
 * @brief Initialisierung des Systems
 * 
 * Diese Funktion wird einmal beim Start ausgeführt und initialisiert alle wichtigen Komponenten.
 */
void setup() {
    stepper.setMaxSpeed(1000); ///< Einstellung des Startwerts für die maximale Geschwindigkeit
    stepper.setAcceleration(1000); ///< Einstellung des Startwerts für die Beschleunigung
    pinMode(PIN_LED_RED, OUTPUT); ///< Initialisierung des Pins der roten LED
    pinMode(PIN_LED_GREEN, OUTPUT); ///< Initialisierung des Pins der grünen LED
    pinMode(PIN_LED_BLUE, OUTPUT); ///< Initialisierung des Pins der blauen LED
    pinMode(PIN_BUTTON, INPUT_PULLUP); ///< Initialisierung des Pins des Tasters
    pinMode(PIN_ENDSTOP, INPUT_PULLUP); ///< Initialisierung des Pins des Endschalters

    Serial.begin(9600); ///< Start der seriellen Kommunikation
    if (!display.begin(SSD1306_SWITCHCAPVCC, SCREEN_ADDRESS)) {
        Serial.println(F("SSD1306 allocation failed"));
        for (;;);
    }

    attachInterrupt(digitalPinToInterrupt(PIN_SW), handleInterrupt, CHANGE); ///< Festlegen eines Interrupts, der das Programm stoppt, sobald er gedrückt wird

    display.display(); ///< Start des Displays, inklusive einer Startanimation von Adafruit
    delay(2000);
    display.setTextSize(2); ///< Festlegung der Textgröße
    display.setTextColor(SSD1306_WHITE); ///< Festlegung der Textfarbe
    updateDisplay(messages[0], messages[4]); ///< Anzeige der Startbenachrichtigung
    delay(1000);
    updateLEDs(false, true, false); ///< Start der LED
}

/**
 * @brief Hauptprogrammschleife
 * 
 * Diese Funktion wird kontinuierlich ausgeführt und steuert die Hauptlogik des Programms.
 */
void loop() {
    long newPosition = encoder.read(); ///< Auswertung der Encoder-Position
    if (newPosition != oldPosition) { ///< Falls die neue Position des Encoders nicht der alten Position des Encoders entspricht
        stage = constrain(newPosition / 4, 1, 10); ///< Übernahme der neuen Position für die Anzeige der Stufe auf dem Bildschirm
        updateDisplay(messages[1], stageMessages[stage]); ///< Anzeige der eingestellten Stufe auf dem Display
        oldPosition = newPosition; ///< Aktualisieren der alten Position
    }

    int buttonReading = digitalRead(PIN_BUTTON); ///< Auswertung des Tasters, ob er gedrückt wurde oder nicht
    if (buttonReading != lastButtonStatus) { ///< Wenn der Zustand des Tasters sich geändert hat
        lastDebounceTime = millis(); ///< Aktualisierung der Zeit, zu der der Taster gedrückt wurde
    }

    if ((millis() - lastDebounceTime) > debounceDelay) { ///< Falls die Zeit zwischen dem Drücken des Tasters größer ist, als die Verzögerung für die Auswertung des Schalters
        if (buttonReading != buttonStatus) { ///< Falls der gespeicherte Status nicht dem tatsächlichen Status des Tasters entspricht
            buttonStatus = buttonReading; ///< Speichern des aktuellen Status des Tasters
            if (buttonStatus == LOW) { ///< Falls der Taster gedrückt wurde
                stepper.setAcceleration(accelerations[0]); ///< Einstellung der Beschleunigung des Motors auf eine angemessene Beschleunigung
                // Schleife zum Finden der Referenzposition
                while (!findReference()) {
                    stepper.setSpeed(-200); ///< Geschwindigkeit des Steppers einstellen
                    stepper.runSpeed(); ///< Einen einzelnen Schritt ausführen
                    // delay(5); ///< Kurze Pause zwischen den Schritten
                }

                int currentStage = stage; ///< Speichern der eingestellten Stufe für den Demonstrationsprozess
                updateDisplay(messages[2], stageMessages[currentStage]); ///< Update des Displays
                updateLEDs(false, false, true); ///< Update der LEDs
                for (int i = 0; i < 2; i++) { ///< Anzahl der auszuführenden Wiederholungen der Demonstration
                    if (i == 0) {
                        stepper.setMaxSpeed(speeds[currentStage]); ///< Einstellung der Geschwindigkeit für die Ausführung der Schritte für den Sicherheitsabstand
                        stepper.setAcceleration(accelerations[currentStage]); ///< Ändern der Beschleunigung basierend auf der Stufe
                        stepper.move(trackLength + safeSteps); ///< Ausführung der Schritte für den Sicherheitsabstand
                        while (stepper.distanceToGo() != 0) {
                          stepper.run();
                        }
                    }
                    else {
                      stepper.setMaxSpeed(speeds[currentStage]); ///< Ändern der Geschwindigkeit basierend auf der Stufe
                      stepper.setAcceleration(accelerations[currentStage]); ///< Ändern der Beschleunigung basierend auf der Stufe
                      stepper.move(trackLength);
                      while (stepper.distanceToGo() != 0) { ///< Ausführung der Bewegung vom Motor weg
                        stepper.run();
                      }
                    }
                    stepper.move(-trackLength);
                    while (stepper.distanceToGo() != 0) { ///< Ausführung der Bewegung zum Motor hin
                        stepper.run();
                    }
                }
                updateDisplay(messages[1], stageMessages[currentStage]); ///< Update des Displays
            }
        }
    }
    lastButtonStatus = buttonReading; ///< Aktualisierung des letzten Status des Tasters
}

/**
 * @brief Aktualisiert die Farbe der LEDs
 * 
 * @param red Gibt an, ob die rote LED an oder aus ist
 * @param green Gibt an, ob die grüne LED an oder aus ist
 * @param blue Gibt an, ob die blaue LED an oder aus ist
 */
void updateLEDs(bool red, bool green, bool blue) {
    digitalWrite(PIN_LED_RED, red ? HIGH : LOW);
    digitalWrite(PIN_LED_GREEN, green ? HIGH : LOW);
    digitalWrite(PIN_LED_BLUE, blue ? HIGH : LOW);
}

/**
 * @brief Aktualisiert das Display basierend auf der eingestellten Nachricht
 * 
 * @param line1 Erste Zeile der Nachricht
 * @param line2 Zweite Zeile der Nachricht (kann leer sein)
 */
void updateDisplay(const char* line1, const char* line2) {
    display.clearDisplay(); ///< Leeren der aktuellen Anzeige des Displays
    display.setCursor(0, 0);
    display.println(F(line1)); ///< Ausgabe der eingestellten Texte auf dem Display
    if (line2 != "") {
        display.println(F(line2));
    }
    display.display();
}

/**
 * @brief Führt die Referenzfahrt aus
 * 
 * @return true Wenn der Referenzpunkt gefunden wurde
 * @return false Wenn der Referenzpunkt noch nicht gefunden wurde
 */
bool findReference() {
    int endstopReading = digitalRead(PIN_ENDSTOP); ///< Auswertung des Endschalters
    if (endstopReading != lastEndstopStatus) { ///< Wenn der Zustand des Endschalters sich geändert hat
        lastEndstopDebounceTime = millis(); ///< Aktualisierung der Zeit, zu der der Endschalter gedrückt wurde
    }

    if ((millis() - lastEndstopDebounceTime) > debounceDelay) { ///< Falls die Zeit zwischen dem Drücken des Endschalters größer ist, als die Verzögerung für die Auswertung des Endschalters
        if (endstopReading != endstopStatus) { ///< Falls der gespeicherte Status nicht dem tatsächlichen Status des Endschalters entspricht
            endstopStatus = endstopReading; ///< Speichern des aktuellen Status des Endschalters
            if (endstopStatus == LOW) { ///< Falls der Endschalter gedrückt wurde
                stepper.stop(); ///< Motor stoppen
                return true; ///< Positive Rückmeldung der Funktion
            }
        }
    }
    lastEndstopStatus = endstopReading; ///< Aktualisierung des letzten Status des Endschalters
    return false; ///< Negative Rückmeldung der Funktion
}

/**
 * @brief Funktion für die Ausführung des Interrupts
 * 
 * Diese Funktion wird aufgerufen, wenn der Encoder-Taster gedrückt wird.
 */
void handleInterrupt() {
    stepper.stop(); ///< Stoppen des Motors
    updateDisplay(messages[3], messages[4]); ///< Aktualisierung der Anzeige auf dem Display
}

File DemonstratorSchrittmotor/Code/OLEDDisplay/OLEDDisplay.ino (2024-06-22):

/**@file */

/**
 * @brief Programm für den Test der Funktionalität eines OLED-Displays

 Beschreibung des Autors:
  
 This is an example for our Monochrome OLEDs based on SSD1306 drivers

 Pick one up today in the adafruit shop!
 ------> http://www.adafruit.com/category/63_98

 This example is for a 128x64 pixel display using I2C to communicate
 3 pins are required to interface (two I2C and one reset).

 Adafruit invests time and resources providing this open
 source code, please support Adafruit and open-source
 hardware by purchasing products from Adafruit!

 Written by Limor Fried/Ladyada for Adafruit Industries,
 with contributions from the open source community.
 BSD license, check license.txt for more information
 All text above, and the splash screen below must be
 included in any redistribution.
 */

#include <SPI.h>
#include <Wire.h>
#include <Adafruit_GFX.h>
#include <Adafruit_SSD1306.h>

#define SCREEN_WIDTH 128 // OLED display width, in pixels
#define SCREEN_HEIGHT 64 // OLED display height, in pixels

// Declaration for an SSD1306 display connected to I2C (SDA, SCL pins)
// The pins for I2C are defined by the Wire-library. 
// On an arduino UNO:       A4(SDA), A5(SCL)
// On an arduino MEGA 2560: 20(SDA), 21(SCL)
// On an arduino LEONARDO:   2(SDA),  3(SCL), ...
#define OLED_RESET     -1 // Reset pin # (or -1 if sharing Arduino reset pin)
#define SCREEN_ADDRESS 0x3C ///< See datasheet for Address; 0x3D for 128x64, 0x3C for 128x32
Adafruit_SSD1306 display(SCREEN_WIDTH, SCREEN_HEIGHT, &Wire, OLED_RESET);

#define NUMFLAKES     10 // Number of snowflakes in the animation example

#define LOGO_HEIGHT   16
#define LOGO_WIDTH    16
static const unsigned char PROGMEM logo_bmp[] =
{ 0b00000000, 0b11000000,
  0b00000001, 0b11000000,
  0b00000001, 0b11000000,
  0b00000011, 0b11100000,
  0b11110011, 0b11100000,
  0b11111110, 0b11111000,
  0b01111110, 0b11111111,
  0b00110011, 0b10011111,
  0b00011111, 0b11111100,
  0b00001101, 0b01110000,
  0b00011011, 0b10100000,
  0b00111111, 0b11100000,
  0b00111111, 0b11110000,
  0b01111100, 0b11110000,
  0b01110000, 0b01110000,
  0b00000000, 0b00110000 };

void setup() {
  Serial.begin(9600);

  // SSD1306_SWITCHCAPVCC = generate display voltage from 3.3V internally
  if(!display.begin(SSD1306_SWITCHCAPVCC, SCREEN_ADDRESS)) {
    Serial.println(F("SSD1306 allocation failed"));
    for(;;); // Don't proceed, loop forever
  }

  // Show initial display buffer contents on the screen --
  // the library initializes this with an Adafruit splash screen.
  display.display();
  delay(2000); // Pause for 2 seconds

  // Clear the buffer
  display.clearDisplay();

  // Draw a single pixel in white
  display.drawPixel(10, 10, SSD1306_WHITE);

  // Show the display buffer on the screen. You MUST call display() after
  // drawing commands to make them visible on screen!
  display.display();
  delay(2000);
  // display.display() is NOT necessary after every single drawing command,
  // unless that's what you want...rather, you can batch up a bunch of
  // drawing operations and then update the screen all at once by calling
  // display.display(). These examples demonstrate both approaches...

  testdrawline();      // Draw many lines

  testdrawrect();      // Draw rectangles (outlines)

  testfillrect();      // Draw rectangles (filled)

  testdrawcircle();    // Draw circles (outlines)

  testfillcircle();    // Draw circles (filled)

  testdrawroundrect(); // Draw rounded rectangles (outlines)

  testfillroundrect(); // Draw rounded rectangles (filled)

  testdrawtriangle();  // Draw triangles (outlines)

  testfilltriangle();  // Draw triangles (filled)

  testdrawchar();      // Draw characters of the default font

  testdrawstyles();    // Draw 'stylized' characters

  testscrolltext();    // Draw scrolling text

  testdrawbitmap();    // Draw a small bitmap image

  // Invert and restore display, pausing in-between
  display.invertDisplay(true);
  delay(1000);
  display.invertDisplay(false);
  delay(1000);

  testanimate(logo_bmp, LOGO_WIDTH, LOGO_HEIGHT); // Animate bitmaps
}

void loop() {
}

void testdrawline() {
  int16_t i;

  display.clearDisplay(); // Clear display buffer

  for(i=0; i<display.width(); i+=4) {
    display.drawLine(0, 0, i, display.height()-1, SSD1306_WHITE);
    display.display(); // Update screen with each newly-drawn line
    delay(1);
  }
  for(i=0; i<display.height(); i+=4) {
    display.drawLine(0, 0, display.width()-1, i, SSD1306_WHITE);
    display.display();
    delay(1);
  }
  delay(250);

  display.clearDisplay();

  for(i=0; i<display.width(); i+=4) {
    display.drawLine(0, display.height()-1, i, 0, SSD1306_WHITE);
    display.display();
    delay(1);
  }
  for(i=display.height()-1; i>=0; i-=4) {
    display.drawLine(0, display.height()-1, display.width()-1, i, SSD1306_WHITE);
    display.display();
    delay(1);
  }
  delay(250);

  display.clearDisplay();

  for(i=display.width()-1; i>=0; i-=4) {
    display.drawLine(display.width()-1, display.height()-1, i, 0, SSD1306_WHITE);
    display.display();
    delay(1);
  }
  for(i=display.height()-1; i>=0; i-=4) {
    display.drawLine(display.width()-1, display.height()-1, 0, i, SSD1306_WHITE);
    display.display();
    delay(1);
  }
  delay(250);

  display.clearDisplay();

  for(i=0; i<display.height(); i+=4) {
    display.drawLine(display.width()-1, 0, 0, i, SSD1306_WHITE);
    display.display();
    delay(1);
  }
  for(i=0; i<display.width(); i+=4) {
    display.drawLine(display.width()-1, 0, i, display.height()-1, SSD1306_WHITE);
    display.display();
    delay(1);
  }

  delay(2000); // Pause for 2 seconds
}

void testdrawrect(void) {
  display.clearDisplay();

  for(int16_t i=0; i<display.height()/2; i+=2) {
    display.drawRect(i, i, display.width()-2*i, display.height()-2*i, SSD1306_WHITE);
    display.display(); // Update screen with each newly-drawn rectangle
    delay(1);
  }

  delay(2000);
}

void testfillrect(void) {
  display.clearDisplay();

  for(int16_t i=0; i<display.height()/2; i+=3) {
    // The INVERSE color is used so rectangles alternate white/black
    display.fillRect(i, i, display.width()-i*2, display.height()-i*2, SSD1306_INVERSE);
    display.display(); // Update screen with each newly-drawn rectangle
    delay(1);
  }

  delay(2000);
}

void testdrawcircle(void) {
  display.clearDisplay();

  for(int16_t i=0; i<max(display.width(),display.height())/2; i+=2) {
    display.drawCircle(display.width()/2, display.height()/2, i, SSD1306_WHITE);
    display.display();
    delay(1);
  }

  delay(2000);
}

void testfillcircle(void) {
  display.clearDisplay();

  for(int16_t i=max(display.width(),display.height())/2; i>0; i-=3) {
    // The INVERSE color is used so circles alternate white/black
    display.fillCircle(display.width() / 2, display.height() / 2, i, SSD1306_INVERSE);
    display.display(); // Update screen with each newly-drawn circle
    delay(1);
  }

  delay(2000);
}
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

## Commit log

2024-04-04 Name geändert
    [DemonstratorSchrittmotor.run.xml]
2024-04-08 Hardwarebeschreibung, TitlePage aktualisiert
    Hardwarebeschreibung fast fertig, fehlt jetzt nur noch Firmware und die zuätzlichen Teile
2024-04-09 Update
    Update vom 09.04.24
    Es fehlt jetzt nur noch die zusätliche Hardware. Ich hab die Firmwarebeschreibung rausgenommen, meiner Meinung nach gehört es zur Softwarebeschreibung.
2024-04-10 Aktuelle Materialliste
    Stand 10 04 24
2024-04-11 Projektbeschreibung
    Habe die Sachen geändert
2024-04-11 upload2_10_04_24
    Es fehlt hier nur noch die Beschreibung der Netzteile und des Schrittmotortreibers.
    Materialliste hab ich jetzt hier auch eingefügt.
2024-04-11 Upload3 Weitere Hardware 11_04_24
    Hab hier jetzt auch die Materialliste gepackt
    Ich hab die Netzteile erst einmal nur dürfig beschrieben
2024-04-12 Update Beschreibung der Software IDE.tex
    Inhalt eingefügt
2024-04-15 Update-Handbuch-15-04-24
    Rechtschreibung und kleinigkeiten geändert
2024-04-15 Update Materialliste.tex
    fehler behoben
2024-04-15 Update and rename Beschreibung der Software IDE.tex to SoftwarebeschreibungIDE.tex
    Dateiname geändert und ein paar Kleinigkeiten.
    Bitte ladet auch nur funktionierende Datein hoch. Verwendet möglichst keine "Anführungszeichen", die sind aufwendig zu schreiben mit Befehl und sehen auch unprofessionel aus. Nehmt lieber Kursivschri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
2024-04-15 Update and rename Beschreibung des Programms auf dem Arduino.tex to SchrittmotorProgrammbeschreibung.tex
2024-04-15 Update and rename Beschreibung des Schrittmotors 28BYJ_48.tex to Schrittmotorbeschreibung.tex
2024-04-15 Delete Template/report/Contents/de/Beschreibung der Hardware des Arduino Nano 33 BLE Sense Lite.tex
    ist 2 mal drinn
2024-04-15 Update Projektplan
    [Projektplan.xlsx]
2024-04-15 Anpassungen und Schrittmotorsteuerung eingefügt
2024-04-18 Add files via upload
    Bipolar- und Unipolarbetrieb sowie Beschreibung des verwendeten Schrittmotors hinzugefügt
2024-04-18 fehlte noch
    ich hab alle Daten, die ich wusste eingefügt, eure personenbezogenen Daten fehlen noch
    [author.xlsx]
2024-04-23 Add files via upload
    ISt der aktualisierte Projektplan
    [Projektplan.xlsx]
2024-04-29 Ordner "Template" gelöscht
    [DemonstratorSchrittmotor.run.xml, HandbuchDemonstratorSchrittmotor.run.xml, Projektplan.xlsx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]
2024-04-29 Update-29-04-24
    Literaturverzeichnis eingebunden und Ordner TEMPLATE aus Präsentation umbenannt
    [output.csv]
2024-04-29 Update README.txt
    Eventuell kann man die detailierte Beschreibung auch ganz weglassen
2024-05-01 Update Bewegungsablauf.tex
    Maik du hast die Datei irgendwie kaputt gemacht, ich habe versucht sie zu reparieren. Du hast anscheinend die Änderungen mit kopiert, sodass alles doppelt drinn war. Ich hoffe es ist jetzt so, wie du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
2024-05-02 Update 02-05-24
    Ich würde Abschnitt Display raus nehmen, das ist auch alles schon in Abschnitt Inbetriebnahme gesagt. Es fehlen aber noch einige Bilder, damit die Anweisungen gut verständlich sind.
2024-05-03 Update SetUp.tex
    Lagerung und Transport hinzugefügt.
2024-05-06 update-06-05-24
    Ich würde den Transport und die Lagerung nicht in die Inbetriebnahme packen. Ich hab das Aufwickeln des Kabels jetzt indirekt drin.
2024-05-06 Stromversorgung geändert.
    Ist jetzt noch doppelt drinn aber ich denke es kann auch nochmal in der Inbetriebnahme erwähnt werden
2024-05-06 Ordner umbenannt
    [DemonstratorSchrittmotor.run.xml]
2024-05-16 Paar Dinge geändert-16-05-24
    @Maik du benutzt hier fast 1 zu 1 den Inhalt der Quelle, ich weiß nicht wie gern Wings das hat, vl kann man das ein bisschen Umschreiben?
2024-05-28 Link geändert
    [author.xlsx]
2024-06-01 Mein Author-Teil vervollständigt
    [author.xlsx]
2024-06-03 Bilder für Materialliste eingefügt
2024-06-03 Bilder in Materialliste muss noch angepasst werden
2024-06-11 update author
    [author.xlsx]
2024-06-12 Literatur hinzugefügt und Kleinigkeiten
2024-06-13 Create MateriallisteQuellen
2024-06-13 Ordner hinzugefügt und kleine Änderungen
    [DemonstratorSchrittmotor.run.xml]
2024-06-14 Update Ordner für Montage und Demontage Anleitung
2024-06-14 Bilder Ref label und positionierung
    [DemonstratorSchrittmotor.run.xml]
2024-06-15 Literaturverzeichnis in TEX
    [A4988 Arduino Nano.fzz, AMS1117Halter.STL, Aluprofil.stp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]
